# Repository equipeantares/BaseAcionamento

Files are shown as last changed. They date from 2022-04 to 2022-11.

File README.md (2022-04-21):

# Base de Acionamento

## Introdução 

### Motivação

A equipe Antares de espaçomodelismo da Unicamp tem como um de seus projetos desenvolvidos o foguete Aurora. Trata-se de um foguete de propulsão sólida com apogeu esperado de 3km. Como parte dos requisitos necessários para ter sucesso na missão, o foguete precisa de um sistema de aviônica que será responsável por coletar dados e tomar decisões previamente programadas durante o voo. Com o objetivo de monitorar o estado do foguete antes, durante e depois do lançamento, é necessário ter um sistema em solo que seja capaz de receber os dados coletados pela aviônica, permitindo que os presentes tenham informações em tempo real. Além disso, esse sistema deve permitir que o acionador do motor seja ligado de forma segura durante o lançamento, não expondo pessoas a riscos.

### Objetivo

Sendo assim, o objetivo deste projeto é desenvolver um sistema de controle de base para o foguete, o qual deve ser capaz de iniciar o lançamento de forma segura e robusta e capaz de receber e apresentar dados da telemetria do voo colhidos pela aviônica.

### Soluções comerciais

Pelo fato de o sistema precisar ser personalizado, se ajustando ao sistema presente no foguete e aos demais requisitos específicos do projeto, não existem alternativas comerciais que cumpram integralmente o objetivo.

## Especificação
    - Microcontrolador: o dispositivo deverá ser capaz de fazer processamentos lógicos, sendo assim necessário um microcontrolador. Por motivos de acessibilidade e familiaridade, será utilizada a plataforma Arduino no MCU ESP-8266 12F.

    - Comunicação e dados: com o objetivo de receber dados de telemetria do foguete, o dispositivo deverá ter um sistema transceptor, que será implementado por um módulo LoRA E32-915T20D.

    - Interface: como interface, o dispositivo contará com pinos auxiliares para monitoramento do funcionamento da placa e pinos de seleção de função para alimentação e modo de acionamento da ignição, sendo a seleção feita por meio de jumpers.

    - Ignição: deverá suportar dois modos de acionamento do circuito ignitor: por sinal elétrico e por comando remoto. O modo será escolhido via inserção manual de jumpers antes do lançamento.

    - Alimentação: o sistema deverá ter interface de alimentação, podendo operar com a alimentação interna de 3V3 ou alimentação externa de 5V.

## Diagrama

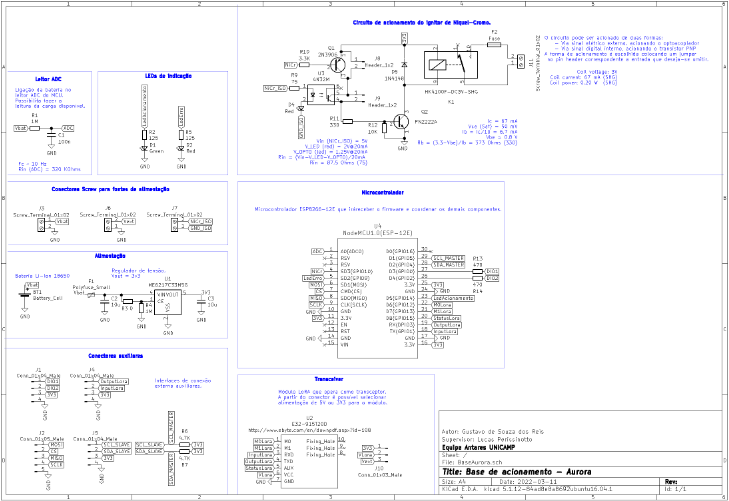
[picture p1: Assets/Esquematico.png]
Esquematico


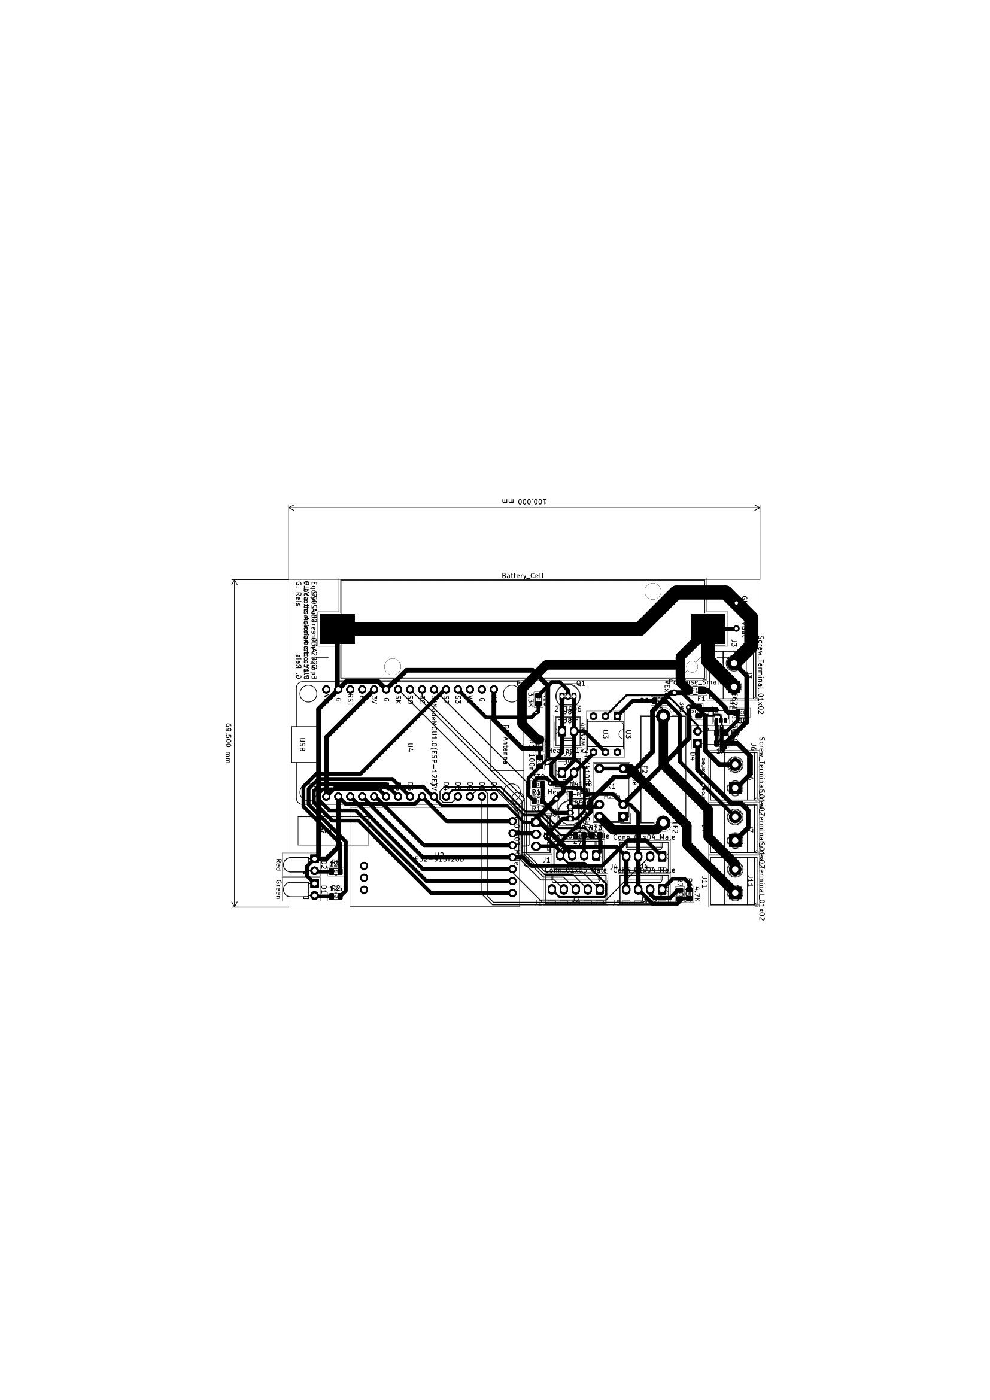
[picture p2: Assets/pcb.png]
Layout PCB


## Pinagem

### Pinout conector Screw bateria 18650

Pino | Sinal
-----|------
1  | VBat
2  | GND

### Pinout conector Screw do Acionamento

Pino | Sinal
-----|------
  1  | NiCr_ISO
  2  | GND_ISO

### Pinout conector Screw Alimentação externa

Pino | Sinal
-----|------
  1  | VExt
  2  | GND

### Pinout conector GPIO aux

Pino | Sinal
-----|------
  1  | DIO1
  2  | DIO2
  3  | 3V3
  4  | GND

### Pinout conector LoRA aux

Pino | Sinal
-----|------
  1  | OutputLora
  2  | InputLora
  3  | 3V3
  4  | GND

### Pinout conector I2C aux

Pino | Sinal
-----|------
  1  | SCL_SLAVE
  2  | SDA_SLAVE
  3  | 3V3
  4  | GND

### Pinout conector SPI aux

Pino | Sinal
-----|------
  1  | MOSI
  2  | CS
  3  | MISO
  4  | SCLK
  5  | GND

### Pinout conector de seleção alimentação LoRA

Pino | Sinal
-----|------
  1  | 3V3
  2  | VLora
  3  | VExt

### Pinout conector Transistor PNP acionamento (interno)

Pino | Sinal
-----|------
  1  | Emissor
  2  | Coletor

### Pinout conector Optoacoplador acionamento (externo)

Pino | Sinal
-----|------
  1  | Coletor
  2  | Emissor

## Testes

    A fim de garantir que o sistema seja seguro e que tudo funcione como esperado, é necessário realizar testes controlados de cada parte do sistema, tentando antecipar possíveis falhas que possam ocorrer. 
    Como o sistema de ignição não pode ter acionamento indesejado, devem ocorrer testes em ambientes adversos, como, por exemplo, com componentes desconectados, e o resultado esperado é que o sistema não ative em nenhuma dessas situações.

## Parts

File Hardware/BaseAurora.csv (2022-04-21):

Reference | Value | Footprint | Datasheet
U2 | E32-915T20D | LoRA:E32-xxxT20D | http://www.ebyte.com/en/downpdf.aspx?id=108
J3 | Screw_Terminal_01x02 | TerminalBlock_Phoenix:TerminalBlock_Phoenix_MKDS-1,5-2_1x02_P5.00mm_Horizontal | ~
BT1 | Battery_Cell | Battery:BatteryHolder_Keystone_1042_1x18650 | ~
U1 | ME6217C33M5G | Package_TO_SOT_SMD:SOT-23-5
C2 | 10u | Capacitor_SMD:C_0805_2012Metric | ~
J6 | Screw_Terminal_01x02 | TerminalBlock_Phoenix:TerminalBlock_Phoenix_MKDS-1,5-2_1x02_P5.00mm_Horizontal | ~
C3 | 10u | Capacitor_SMD:C_0805_2012Metric | ~
R4 | 1M | Resistor_SMD:R_0805_2012Metric | ~
R3 | 0 | Resistor_SMD:R_0805_2012Metric | ~
J10 | Conn_01x03_Male | Connector_Molex:Molex_KK-254_AE-6410-03A_1x03_P2.54mm_Vertical | ~
R11 | 330 | Resistor_SMD:R_0805_2012Metric | ~
R12 | 10K | Resistor_SMD:R_0805_2012Metric | ~
R9 | 75 | Resistor_SMD:R_0805_2012Metric | ~
D5 | 1N4148 | Diode_SMD:D_SOD-123 | ~
F1 | Polyfuse_Small | Fuse:Fuse_1206_3216Metric_Castellated | ~
R1 | 1M | Resistor_SMD:R_0805_2012Metric | ~
D1 | Green | LED_THT:LED_D3.0mm_Horizontal_O1.27mm_Z2.0mm | ~
R2 | 125 | Resistor_SMD:R_0805_2012Metric | ~
D2 | Red | LED_THT:LED_D3.0mm_Horizontal_O1.27mm_Z2.0mm | ~
R5 | 125 | Resistor_SMD:R_0805_2012Metric | ~
J4 | Conn_01x04_Male | Connector_Molex:Molex_KK-254_AE-6410-04A_1x04_P2.54mm_Vertical | ~
J5 | Conn_01x04_Male | Connector_Molex:Molex_KK-254_AE-6410-04A_1x04_P2.54mm_Vertical | ~
R13 | 470 | Resistor_SMD:R_0805_2012Metric | ~
R14 | 470 | Resistor_SMD:R_0805_2012Metric | ~
J1 | Conn_01x04_Male | Connector_Molex:Molex_KK-254_AE-6410-04A_1x04_P2.54mm_Vertical | ~
J11 | Screw_Terminal_01x02 | TerminalBlock_Phoenix:TerminalBlock_Phoenix_MKDS-1,5-2_1x02_P5.00mm_Horizontal | ~
F2 | Fuse | Fuse:Fuseholder_Cylinder-5x20mm_Stelvio-Kontek_PTF78_Horizontal_Open | ~
Q2 | PN2222A | Package_TO_SOT_THT:TO-92_Inline | https://www.onsemi.com/pub/Collateral/PN2222-D.PDF
K1 | HK4100F-DC3V-SHG | Relay_THT:Relay_SPDT_Omron_G5V-1 | http://omronfs.omron.com/en_US/ecb/products/pdf/en-g5v_1.pdf
J9 | Header_1x2 | Connector_Molex:Molex_KK-254_AE-6410-02A_1x02_P2.54mm_Vertical | ~
J8 | Header_1x2 | Connector_Molex:Molex_KK-254_AE-6410-02A_1x02_P2.54mm_Vertical | ~
R10 | 3.3K | Resistor_SMD:R_0805_2012Metric | ~
U3 | 4N32M | Package_DIP:DIP-6_W7.62mm | https://www.vishay.com/docs/83725/4n25.pdf
Q1 | 2N3906 | Package_TO_SOT_THT:TO-92_Inline | https://www.onsemi.com/pub/Collateral/2N3906-D.PDF
C1 | 100n | Capacitor_SMD:C_0805_2012Metric | ~
J2 | Conn_01x05_Male | Connector_Molex:Molex_KK-254_AE-6410-05A_1x05_P2.54mm_Vertical | ~
R7 | 4.7K | Resistor_SMD:R_0805_2012Metric | ~
R6 | 4.7K | Resistor_SMD:R_0805_2012Metric | ~
J7 | Screw_Terminal_01x02 | TerminalBlock_Phoenix:TerminalBlock_Phoenix_MKDS-1,5-2_1x02_P5.00mm_Horizontal | ~
D4 | Red | LED_THT:LED_D3.0mm_Horizontal_O1.27mm_Z2.0mm | ~
U4 | NodeMCU1.0(ESP-12E) | ESP8266:ESP12F-Devkit-V3

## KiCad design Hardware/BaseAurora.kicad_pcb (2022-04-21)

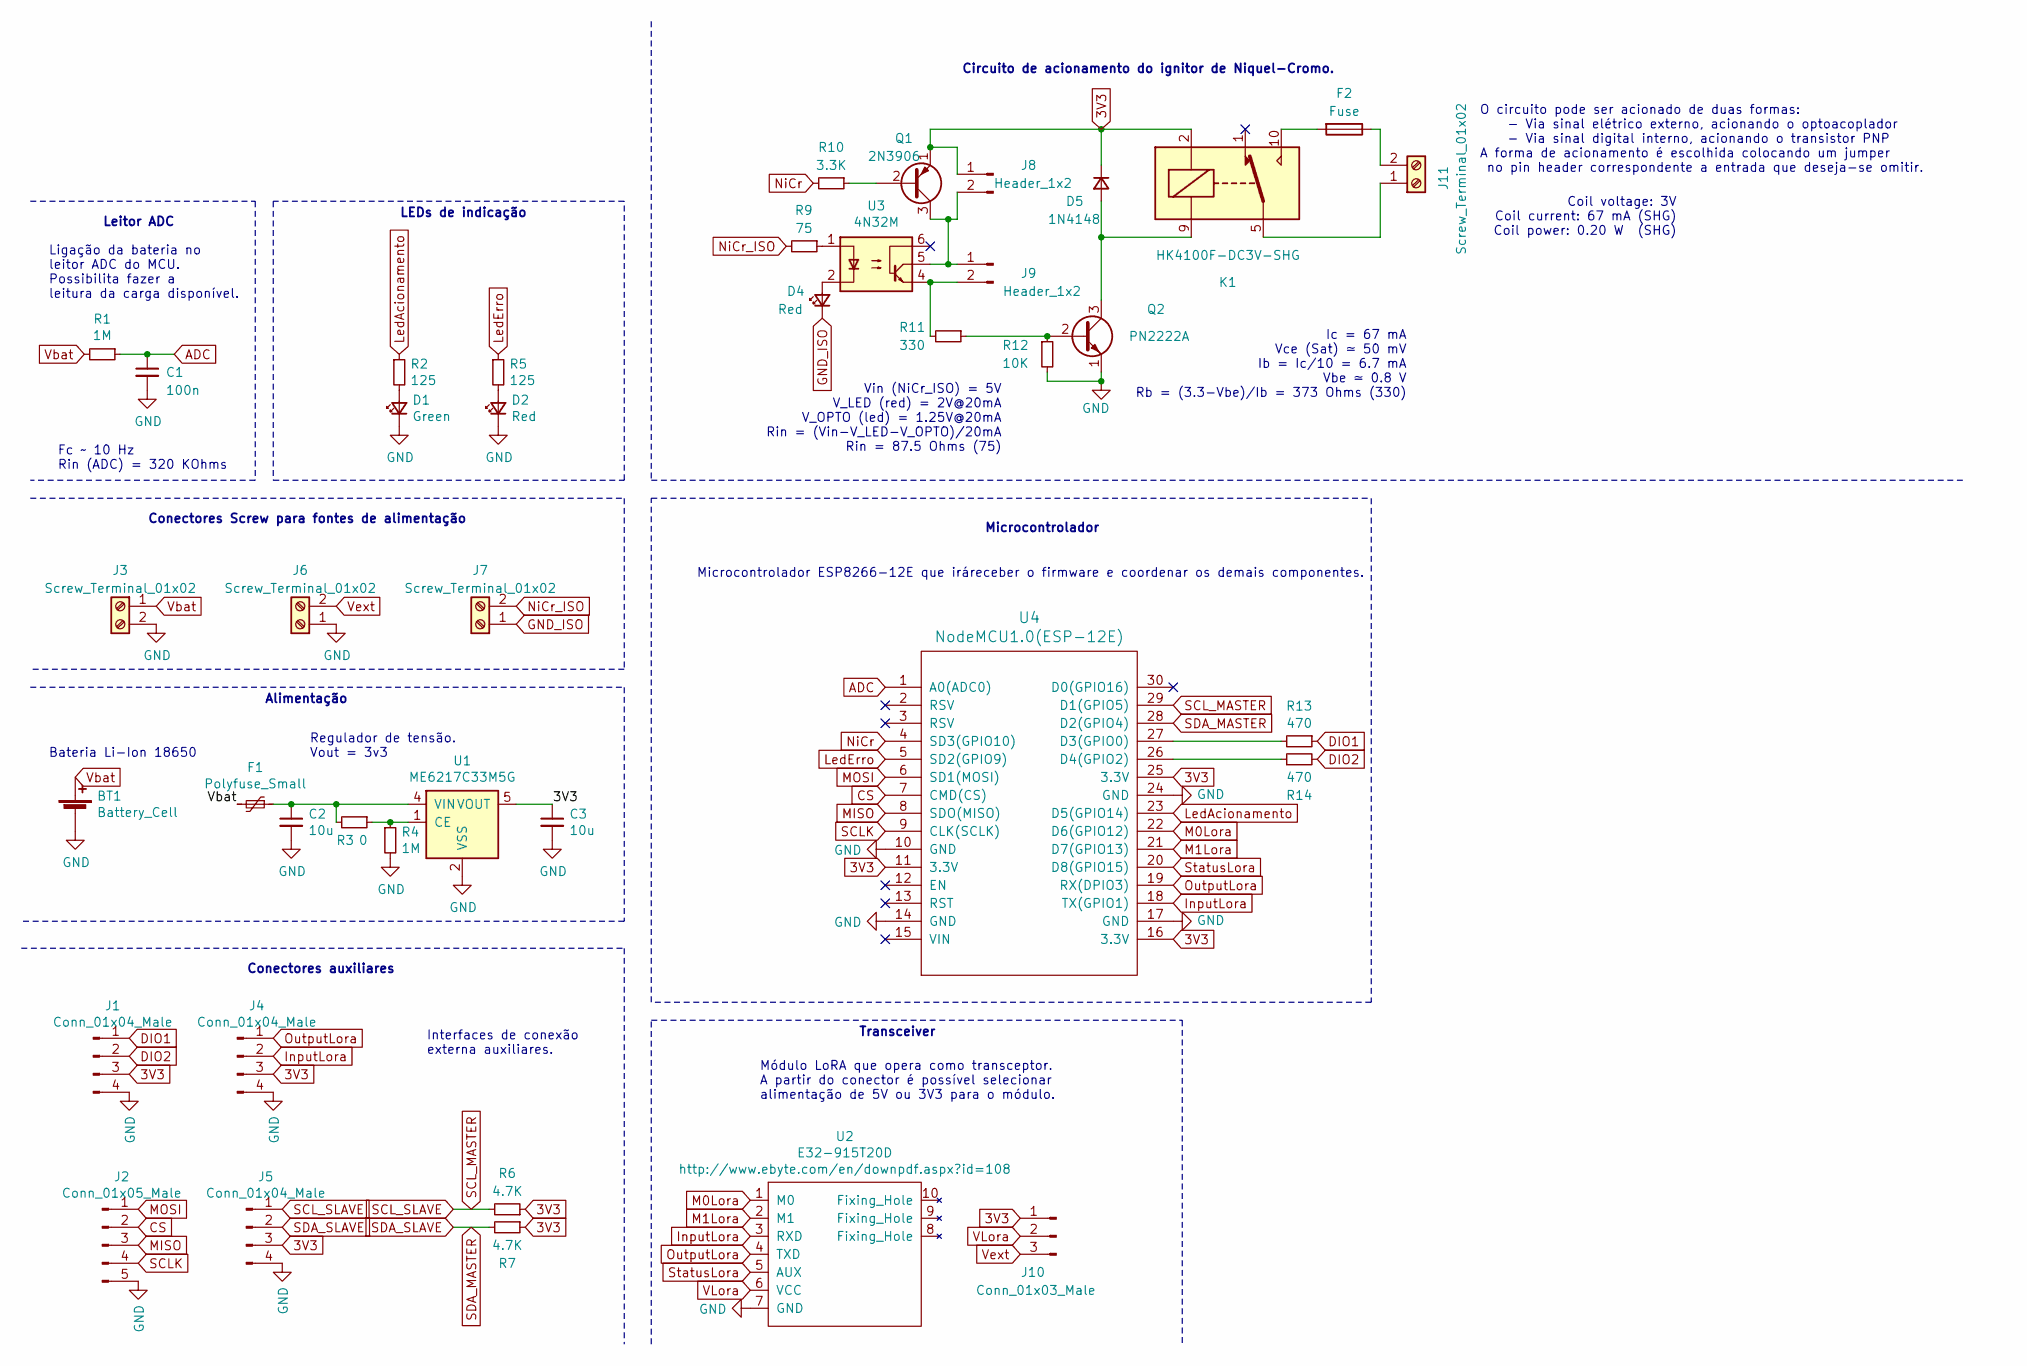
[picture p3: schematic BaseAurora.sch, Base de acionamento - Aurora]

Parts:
BT1: Battery_Cell; BatteryHolder_Keystone_1042_1x18650
C1: 100n; C_0805_2012Metric
C2, C3: 10u; C_0805_2012Metric
D1: Green; LED_D3.0mm_Horizontal_O1.27mm_Z2.0mm
D2, D4: Red; LED_D3.0mm_Horizontal_O1.27mm_Z2.0mm
D5: 1N4148; D_SOD-123
F1: Polyfuse_Small; Fuse_1206_3216Metric_Castellated
F2: Fuse; Fuseholder_Cylinder-5x20mm_Stelvio-Kontek_PTF78_Horizontal_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
J1, J4, J5: Conn_01x04_Male; Molex_KK-254_AE-6410-04A_1x04_P2.54mm_Vertical
J2: Conn_01x05_Male; Molex_KK-254_AE-6410-05A_1x05_P2.54mm_Vertical
J3, J6, J7, J11: Screw_Terminal_01x02; TerminalBlock_Phoenix_MKDS-1,5-2_1x02_P5.00mm_Horizontal
J8, J9: Header_1x2; Molex_KK-254_AE-6410-02A_1x02_P2.54mm_Vertical
J10: Conn_01x03_Male; Molex_KK-254_AE-6410-03A_1x03_P2.54mm_Vertical
K1: HK4100F-DC3V-SHG; Relay_SPDT_Omron_G5V-1
Q1: 2N3906; TO-92_Inline
Q2: PN2222A; TO-92_Inline
R1, R4: 1M; R_0805_2012Metric
R2, R5: 125; R_0805_2012Metric
R3: 0; R_0805_2012Metric
R6, R7: 4.7K; R_0805_2012Metric
R9: 75; R_0805_2012Metric
R10: 3.3K; R_0805_2012Metric
R11: 330; R_0805_2012Metric
R12: 10K; R_0805_2012Metric
R13, R14: 470; R_0805_2012Metric
U1: ME6217C33M5G; SOT-23-5
U2: E32-915T20D; E32-xxxT20D
U3: 4N32M; DIP-6_W7.62mm
U4: NodeMCU1.0(ESP-12E); ESP12F-Devkit-V3

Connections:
3V3: C3.1, D5.1 (K), J1.3, J4.3, J5.3, J8.1, J10.1, K1.2, Q1.1 (E), R6.1, R7.1, U1.5 (VOUT), U4.11 (3.3V), U4.16 (3.3V), U4.25 (3.3V)
ADC: C1.1, R1.1, U4.1 (A0(ADC0))
CS: J2.2, U4.7 (CMD(CS))
DIO1: J1.1, R13.1
DIO2: J1.2, R14.2
GND: BT1.2 (-), C1.2, C2.2, C3.2, D1.1 (K), D2.1 (K), J1.4, J2.5, J3.2, J4.4, J5.4, J6.1, Q2.1 (E), R4.2, R12.2, U1.2 (VSS), U2.7 (GND), U4.10 (GND), U4.14 (GND), U4.17 (GND), U4.24 (GND)
GND_ISO: D4.1 (K), J7.1
InputLora: J4.2, U2.3 (RXD), U4.18 (TX(GPIO1))
LedAcionamento: R2.1, U4.23 (D5(GPIO14))
LedErro: R5.1, U4.5 (SD2(GPIO9))
M0Lora: U2.1 (M0), U4.22 (D6(GPIO12))
M1Lora: U2.2 (M1), U4.21 (D7(GPIO13))
MISO: J2.3, U4.8 (SDO(MISO))
MOSI: J2.1, U4.6 (SD1(MOSI))
unnamed: C2.1, F1.1, R3.2, U1.4 (VIN)
unnamed: D1.2 (A), R2.2
unnamed: D2.2 (A), R5.2
unnamed: D4.2 (A), U3.2
unnamed: D5.2 (A), K1.9, Q2.3 (C)
unnamed: F2.1, J11.2
unnamed: F2.2, K1.10
unnamed: J8.2, J9.1, Q1.3 (C), U3.5
unnamed: J9.2, R11.2, U3.4
unnamed: J11.1, K1.5, K1.6
unnamed: Q1.2 (B), R10.1
unnamed: Q2.2 (B), R11.1, R12.1
unnamed: R3.1, R4.1, U1.1 (CE)
unnamed: R9.1, U3.1
unnamed: R13.2, U4.27 (D3(GPIO0))
unnamed: R14.1, U4.26 (D4(GPIO2))
NiCr: R10.2, U4.4 (SD3(GPIO10))
NiCr_ISO: J7.2, R9.2
OutputLora: J4.1, U2.4 (TXD), U4.19 (RX(DPIO3))
SCLK: J2.4, U4.9 (CLK(SCLK))
SCL_MASTER: J5.1, R6.2, U4.29 (D1(GPIO5))
SDA_MASTER: J5.2, R7.2, U4.28 (D2(GPIO4))
StatusLora: U2.5 (AUX), U4.20 (D8(GPIO15))
VLora: J10.2, U2.6 (VCC)
Vbat: BT1.1 (+), F1.2, J3.1, R1.2
Vext: J6.2, J10.3

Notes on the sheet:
Coil voltage: 3V Coil current: 67 mA (SHG) Coil power: 0.20 W (SHG)
Ic = 67 mA Vce (Sat) ≃ 50 mV Ib = Ic/10 = 6.7 mA Vbe ≃ 0.8 V Rb = (3.3-Vbe)/Ib = 373 Ohms (330)
Vin (NiCr_ISO) = 5V V_LED (red) = 2V@20mA V_OPTO (led) = 1.25V@20mA Rin = (Vin-V_LED-V_OPTO)/20mA Rin = 87.5 Ohms (75)
Fc ~~ 10 Hz Rin (ADC) = 320 KOhms
Interfaces de conexão externa auxiliares.
Regulador de tensão. Vout = 3v3
Conectores Screw para fontes de alimentação
LEDs de indicação
Ligação da bateria no leitor ADC do MCU. Possibilita fazer a leitura da carga disponível.
Módulo LoRA que opera como transceptor. A partir do conector é possível selecionar alimentação de 5V ou 3V3 para o módulo.
Microcontrolador ESP8266-12E que iráreceber o firmware e coordenar os demais componentes.
O circuito pode ser acionado de duas formas: - Via sinal elétrico externo, acionando o optoacoplador - Via sinal digital interno, acionando o transistor PNP A forma de acionamento é escolhida colocando um jumper no pin header correspondente a entrada que deseja-se omitir.
Circuito de acionamento do ignitor de Niquel-Cromo.
Microcontrolador
Transceiver
Conectores auxiliares
Bateria Li-Ion 18650
Alimentação
Leitor ADC

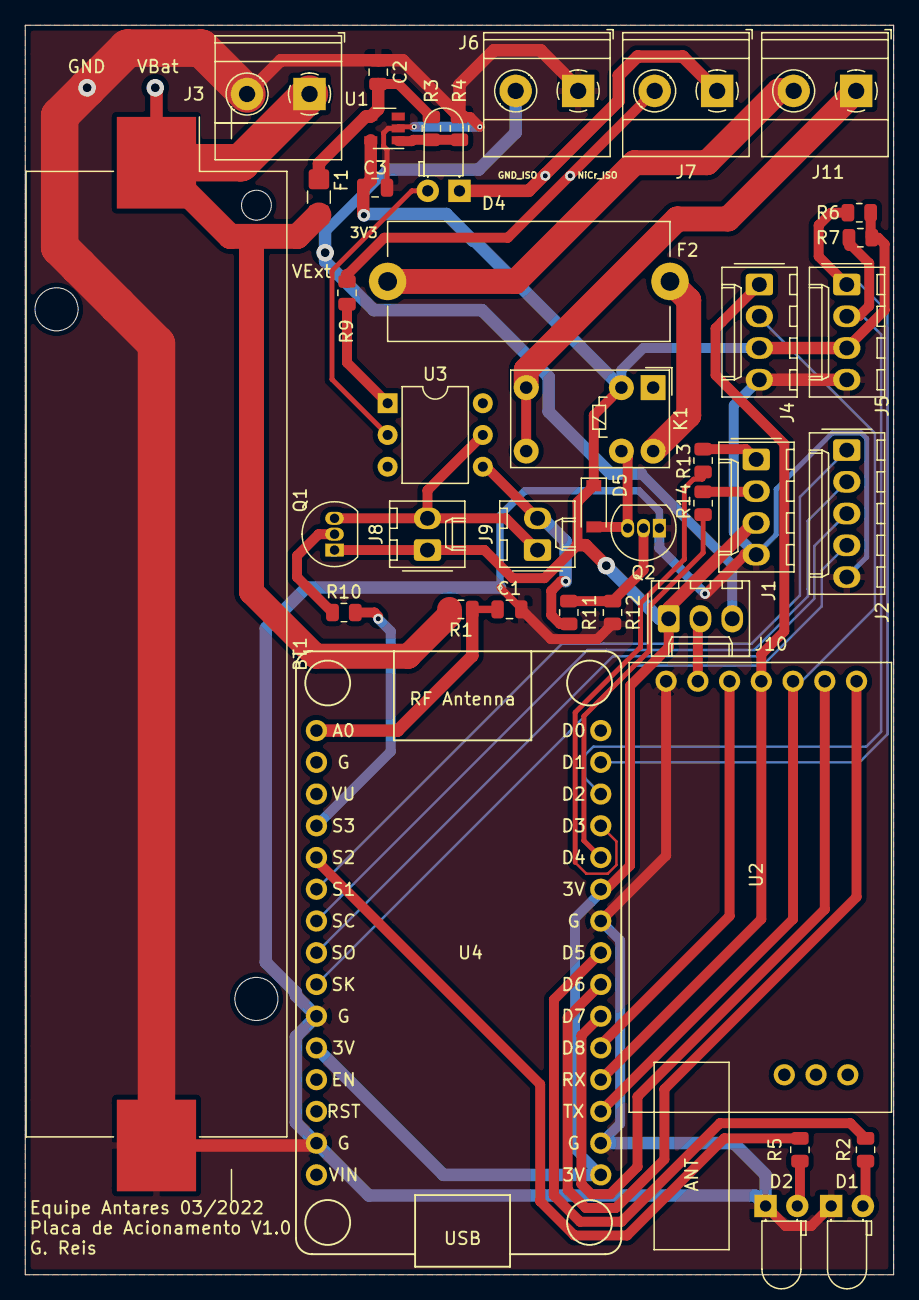
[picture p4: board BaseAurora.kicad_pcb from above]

Board: 2 copper layers, 69.5 x 100.0 mm, 41 parts (0 on the bottom side), 40 nets.

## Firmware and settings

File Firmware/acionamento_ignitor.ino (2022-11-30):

#define pinoIgn 10
#define ledIgn  14  

void setup(){
  //setup
  pinMode(12,OUTPUT);
  digitalWrite(12,LOW);
  pinMode(13,OUTPUT);
  digitalWrite(13,LOW);
  pinMode(pinoIgn, OUTPUT);
  digitalWrite(pinoIgn, HIGH);
  pinMode(ledIgn, OUTPUT);

  delay(5000);
  
  Serial.begin(9600);


  while (Serial.readString() != "s\n"){
    Serial.println("Comunicacao estabelecida. Digite 's' para iniciar!");
    yield();}

 
  
}

void loop(){

  Serial.println("Sistema de igniçao iniciado");
  Serial.println("Digite a senha:");
  
  while (Serial.readString() != "Kabum"){yield();}

  Serial.println("Igniçao liberada, digite 'i' para ignitar!");
  while (Serial.read() != 'i'){yield();}
  
  Serial.println("Igniçao iniciada");
  for (int i = 0; i < 5; i++){
    digitalWrite(pinoIgn, LOW);
    digitalWrite(ledIgn, HIGH);
    Serial.println("Ignitor ativado");
    delay(5000);
    digitalWrite(pinoIgn, HIGH);
    digitalWrite(ledIgn, LOW);
    delay(5000);
  }
  
  Serial.println("Igniçao finalizada, digite 'n' para iniciar uma nova rotina.'");

  while(Serial.read() != 'n'){yield();}
}

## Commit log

2022-03-04 commit inicial
    [BaseAurora.kicad_pcb, BaseAurora.sch]
2022-03-08 esquematico revisado
    [BaseAurora.sch]
2022-03-10 Revisão do circuito de acionamento. Atribuição de valores para os componentes. Organização geral do esquemático.
    [BaseAurora.sch]
2022-03-11 Reorganização dos componentes e posicionamento do acionamento do NiCr no pino seguro.
    [BaseAurora.sch]
2022-03-16 Design inicial da pcb
    [BaseAurora.sch]
2022-03-18 Refatoração do component placement e design das tracks seguindo o novo fator de forma. Exclusão de um dos leds e reposicionamento da conexão NiCr.
    [BaseAurora.kicad_pcb, BaseAurora.sch]
2022-03-18 Adiciona silk com o logo da equipe
    [BaseAurora.kicad_pcb]
2022-03-21 Correção do design de acordo com o DRC
    [BaseAurora.kicad_pcb]
2022-03-22 Adiciona CSV da BOM e vias de test points
    [BaseAurora.csv, BaseAurora.kicad_pcb]
2022-03-28 Arquivos finais para fabricação
    [BaseAurora-B_Cu.gbr, BaseAurora-B_Mask.gbr, BaseAurora-B_SilkS.gbr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]
2022-11-30 Separa os arquivos em hardware e firmware e adiciona o código do firmware
    [BaseAurora-B_Cu.gbr, BaseAurora-B_Mask.gbr, BaseAurora-B_SilkS.gbr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]
